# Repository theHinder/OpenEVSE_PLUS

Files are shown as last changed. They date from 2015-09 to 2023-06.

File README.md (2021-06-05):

# OpenEVSE_PLUS
README.md for OpenEVSE Hardware
Files SCH and BRD in Eagle format
License CC BY-SA 3.0
OpenEVSE Hardware

Current Version OpenEVSE_PLUS_v5.5.

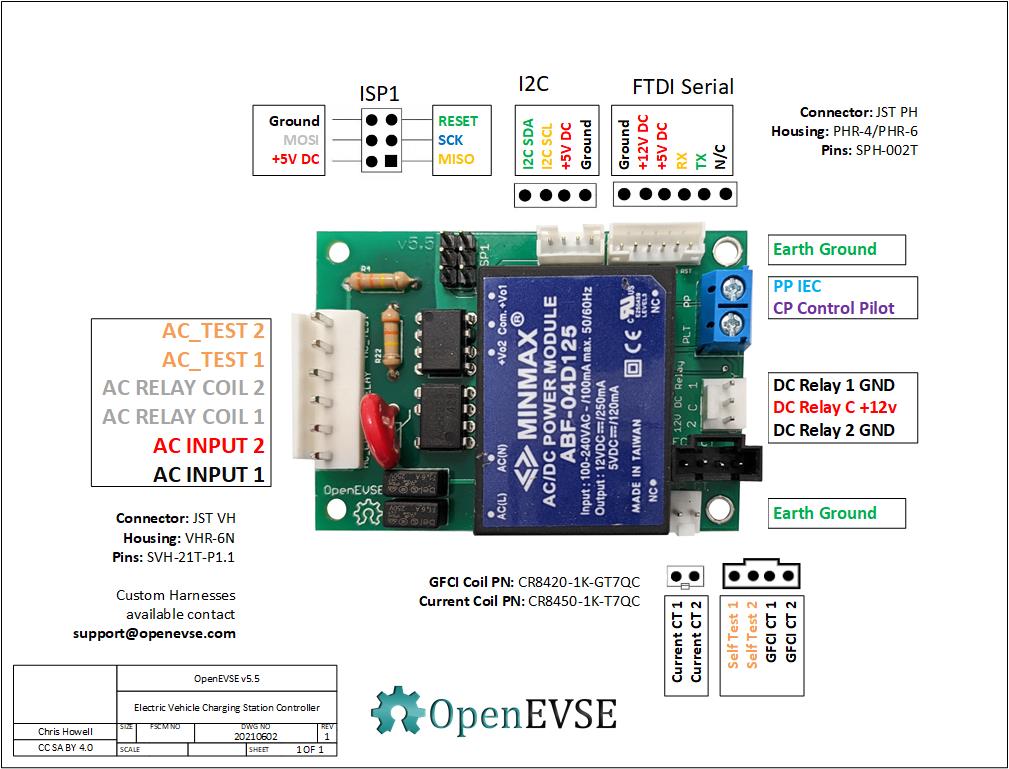
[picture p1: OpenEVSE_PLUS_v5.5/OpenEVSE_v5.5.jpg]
OpenEVSE Electric Vehicle controller v5.5 SAE J1772 IEC 61851


OpenEVSE_PLUS_V5.5 - Moved GFCI Test pin to enable move of DC Relay outputs to PWM capable pins supporting full power closing reduced power holding in OpenEVSE 7.1.2+ firmware. Added GPIO pin pulled HIGH to auto detect board version in software to automatically set new/old pin values without requiring different firmware. Replaced 0.1" generic non-polarized connectors with JST PH for Serial (WiFi) and i2c (Display). Combined power and data connections for WiFi to reduce eliminate a screw terminal connector and simplify wiring harness. Replaced DC/DC converter with a TC1044S invert chip to generate -12v from +12v. 

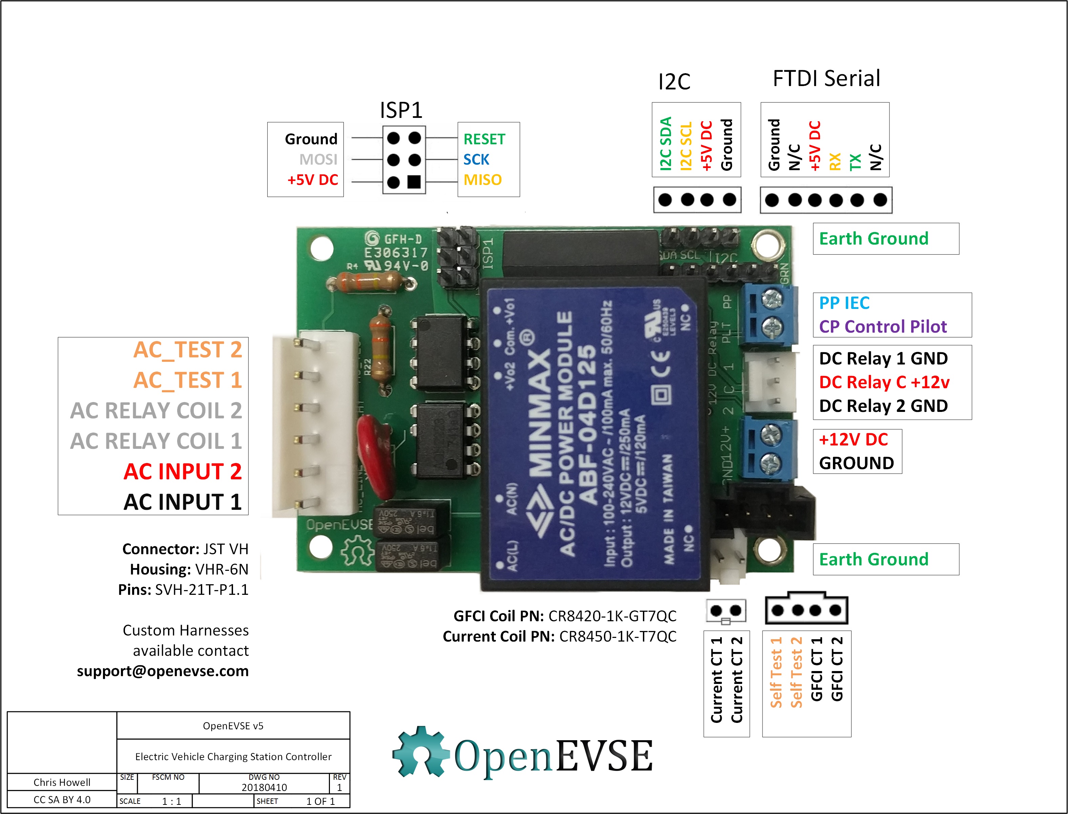
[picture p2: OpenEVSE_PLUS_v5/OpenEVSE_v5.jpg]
OpenEVSE Electric Vehicle controller v5 SAE J1772 IEC 61851


OpenEVSE_PLUS_v5 - Optimized for reduced build time and high volume manufacturing of changing stations, removed most screw terminals and replaced with common connectors. Change from 2 single chanel opto-isolators for AC detection to 1 dual channel. Added ground connections to screw holes.

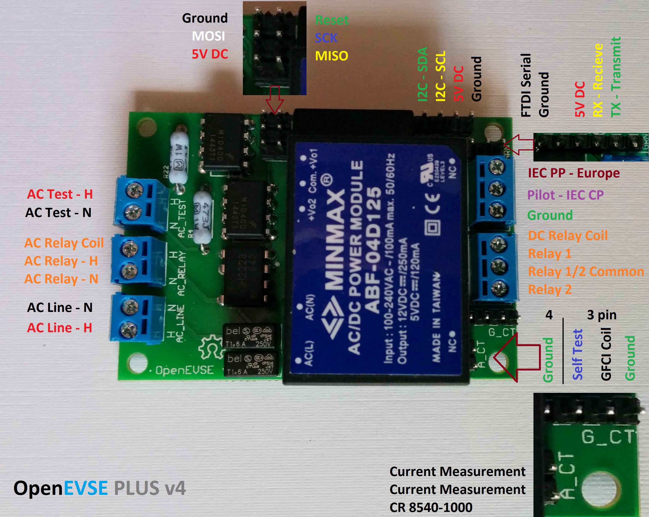
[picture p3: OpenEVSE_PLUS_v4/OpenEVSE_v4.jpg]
OpenEVSE Electric Vehicle controller v4 SAE J1772 IEC 61851


OpenEVSE_PLUS_v4 - Has 2 AC Detect chips like v1 + v2 plus the AC relay driver of v3. Added rectifier diodes to AC detect to improve detection in some conditions. Changed GFCI to individual pinout 4 pins.

OpenEVSE_PLUS_v3 - Removed 1 AC Detect chip and added AC relay driver. Added Current measurement circuit

OpenEVSE_PLUS_v2.5 - Added Current measurement circuit.

OpenEVSE_PLUS_v2 - modified GFCI pinout

OpenEVSE_PLUS_v1 - Inital version - Combined OpenEVSE v7 board and Advanced power supply into single board

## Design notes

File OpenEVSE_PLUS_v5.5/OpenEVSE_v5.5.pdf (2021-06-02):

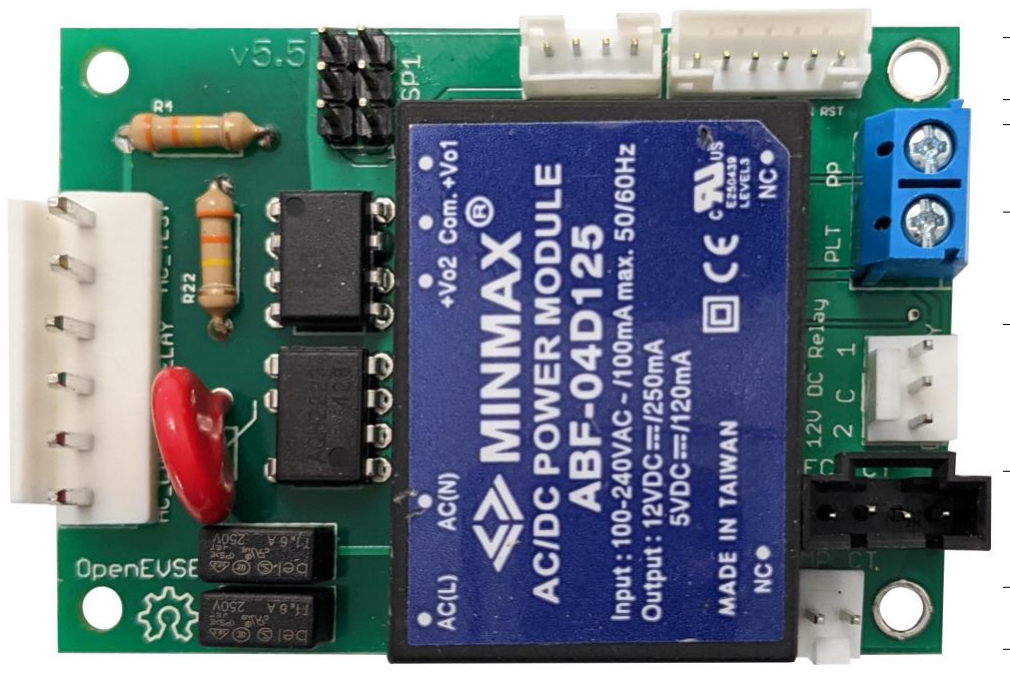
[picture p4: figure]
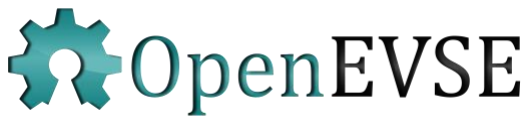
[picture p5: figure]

Chris Howell Chris Howell | SIZE SIZE | FSCM NO FSCM NO | DWG NO DWG NO | REV REV
| | | 20210602 20210602 | 1 1
CC SA BY 4.0 CC SA BY 4.0 | SCALE SCALE | | | SHEET SHEET | 1 OF 1 1 OF 1

OpenEVSE v5.5

Electric Vehicle Charging Station Controller

OpenEVSE v5.5

Electric Vehicle Charging Station Controller

## AC_TEST 2 AC_TEST 1 AC RELAY COIL 2 AC RELAY COIL 1 AC INPUT 2 AC INPUT 1

PP IEC
CP Control Pilot

### Earth Ground

### Earth Ground

### DC Relay 1 GND

DC Relay C +12v

### DC Relay 2 GND

I2C SDA
I2C SCL

+5V DC

Ground

Ground

+12V DC
+5V DC

RX
TX

N/C

I2C | FTDI Serial

RESET
SCK
MISO

Ground
MOSI
+5V DC

## ISP1

Current CT 1

Current CT 2

Self Test 1
Self Test 2

GFCI CT 1
GFCI CT 2

Connector: JST VH
Housing: VHR-6N
Pins: SVH-21T-P1.1

Custom Harnesses
available contact
support@openevse.com

GFCI Coil PN: CR8420-1K-GT7QC Current Coil PN: CR8450-1K-T7QC

Connector: JST PH
Housing: PHR-4/PHR-6
Pins: SPH-002T

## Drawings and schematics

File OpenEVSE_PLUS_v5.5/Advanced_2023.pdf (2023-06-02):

## LCD

## LCD

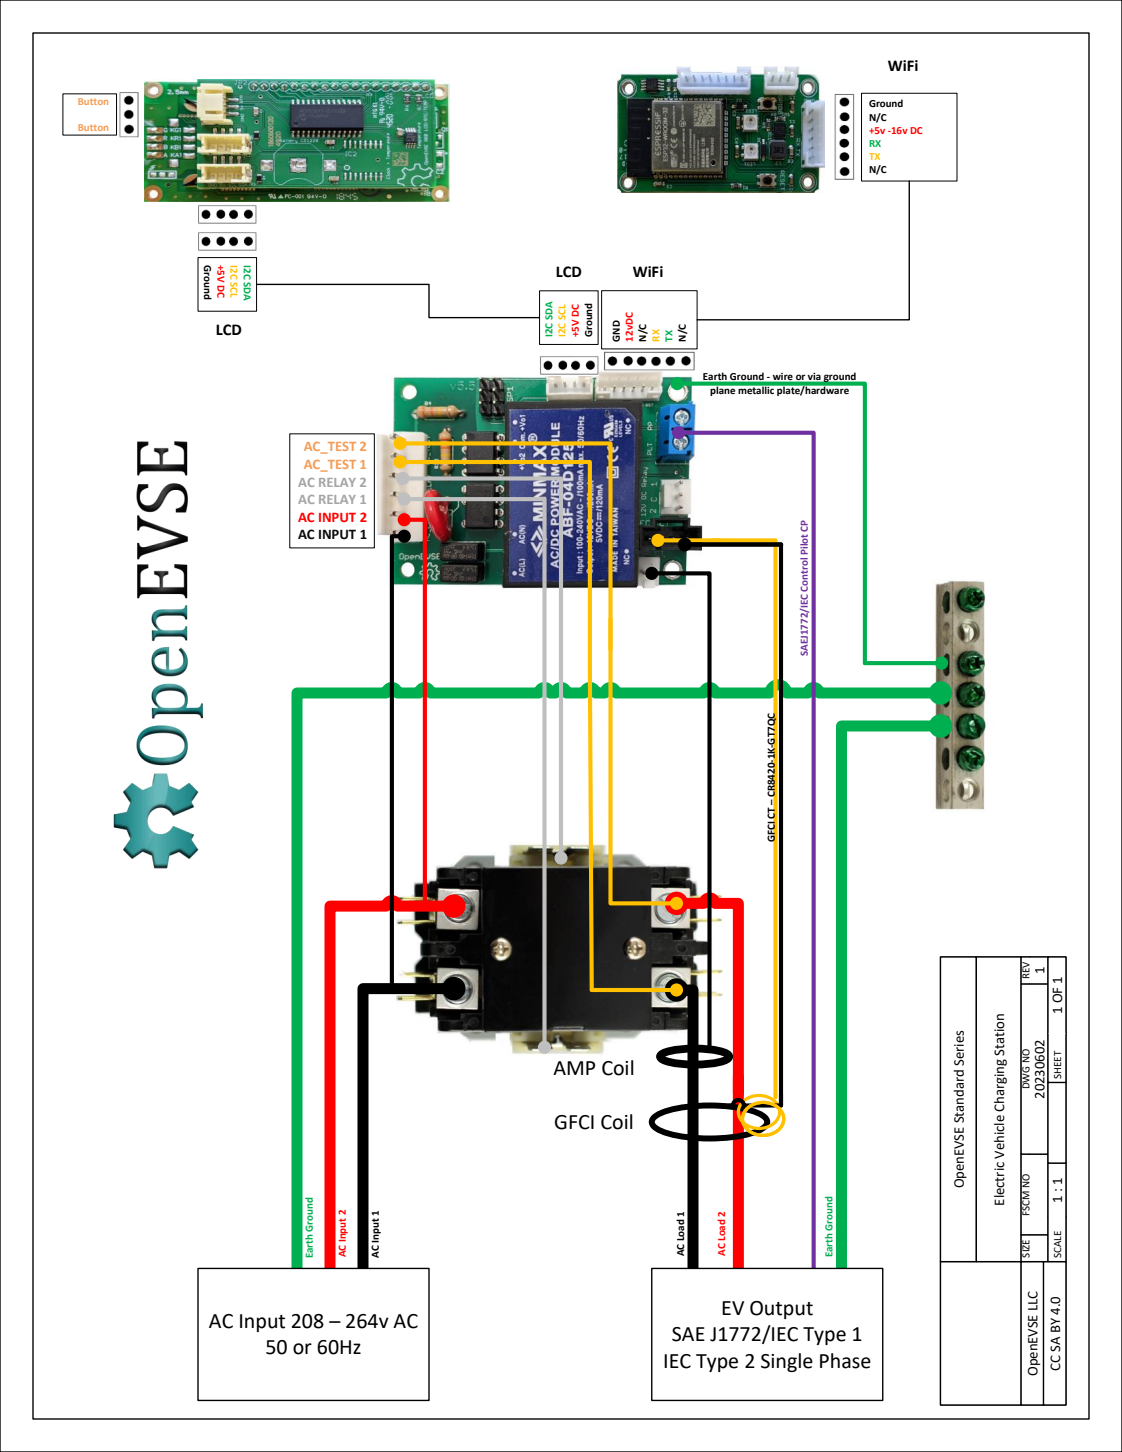
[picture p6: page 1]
I2C SDA; I2C SCL; Ground; Button; AC_TEST 2 AC_TEST 1 AC RELAY 2 AC RELAY 1 AC INPUT 2 AC INPUT 1; GFCI CT – CR8420-1K-GT7QC; Earth Ground; AC Input 2; AC Input 1; AC Load 1; AC Load 2; OpenEVSE LLC; GND; 12vDC; WiFi; Ground N/C +5v -16v DC RX TX N/C; GFCI Coil; AMP Coil

Earth Ground - wire or via ground
plane metallic plate/hardware

SAEJ1772/IEC Control Pilot CP

SIZE FSCM NO DWG NO REV

SCALE 1 : 1 SHEET 1 OF 1

Electric Vehicle Charging Station

OpenEVSE Standard Series

AC Input 208 – 264v AC

EV Output
SAE J1772/IEC Type 1
IEC Type 2 Single Phase

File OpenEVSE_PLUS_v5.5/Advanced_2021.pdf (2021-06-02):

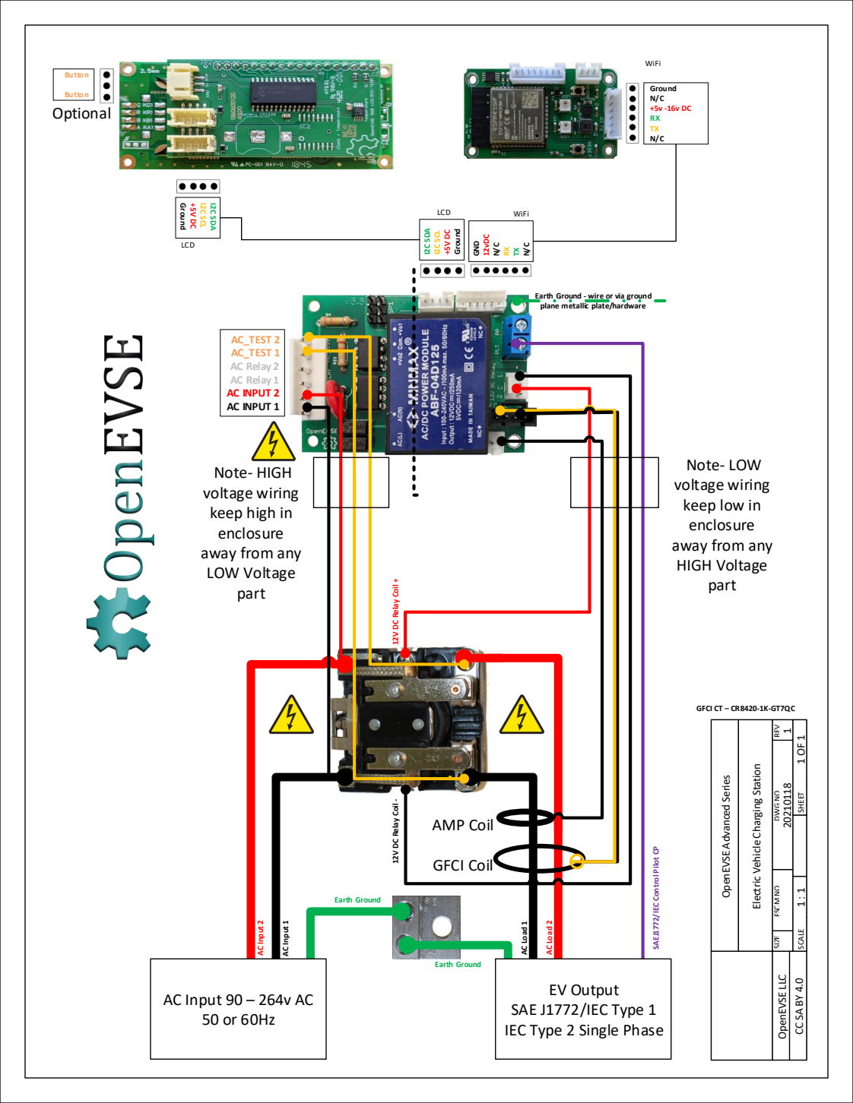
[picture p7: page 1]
I2C SDA; I2C SCL; Ground; GND; 12vDC; LCD; WiFi; Button; Ground N/C +5v -16v DC RX TX N/C; AC_TEST 2 AC_TEST 1 AC Relay 2 AC Relay 1 AC INPUT 2 AC INPUT 1; GFCI CT – CR8420-1K-GT7QC; AC Input 2; AC Input 1; AC Load 1; AC Load 2; Earth Ground; OpenEVSE LLC; Optional; GFCI Coil; AMP Coil

Earth Ground - wire or via ground
plane metallic plate/hardware

Note- LOW
voltage wiring
keep low in
enclosure
away from any
HIGH Voltage
part

Note- HIGH
keep high in
LOW Voltage

12V DC Relay Coil + 12V DC Relay Coil -

SIZE FSCM NO DWG NO REV

SCALE 1 : 1 SHEET 1 OF 1

Electric Vehicle Charging Station

OpenEVSE Advanced Series

SAEJ1772/IEC Control Pilot CP

EV Output
SAE J1772/IEC Type 1
IEC Type 2 Single Phase

AC Input 90 – 264v AC

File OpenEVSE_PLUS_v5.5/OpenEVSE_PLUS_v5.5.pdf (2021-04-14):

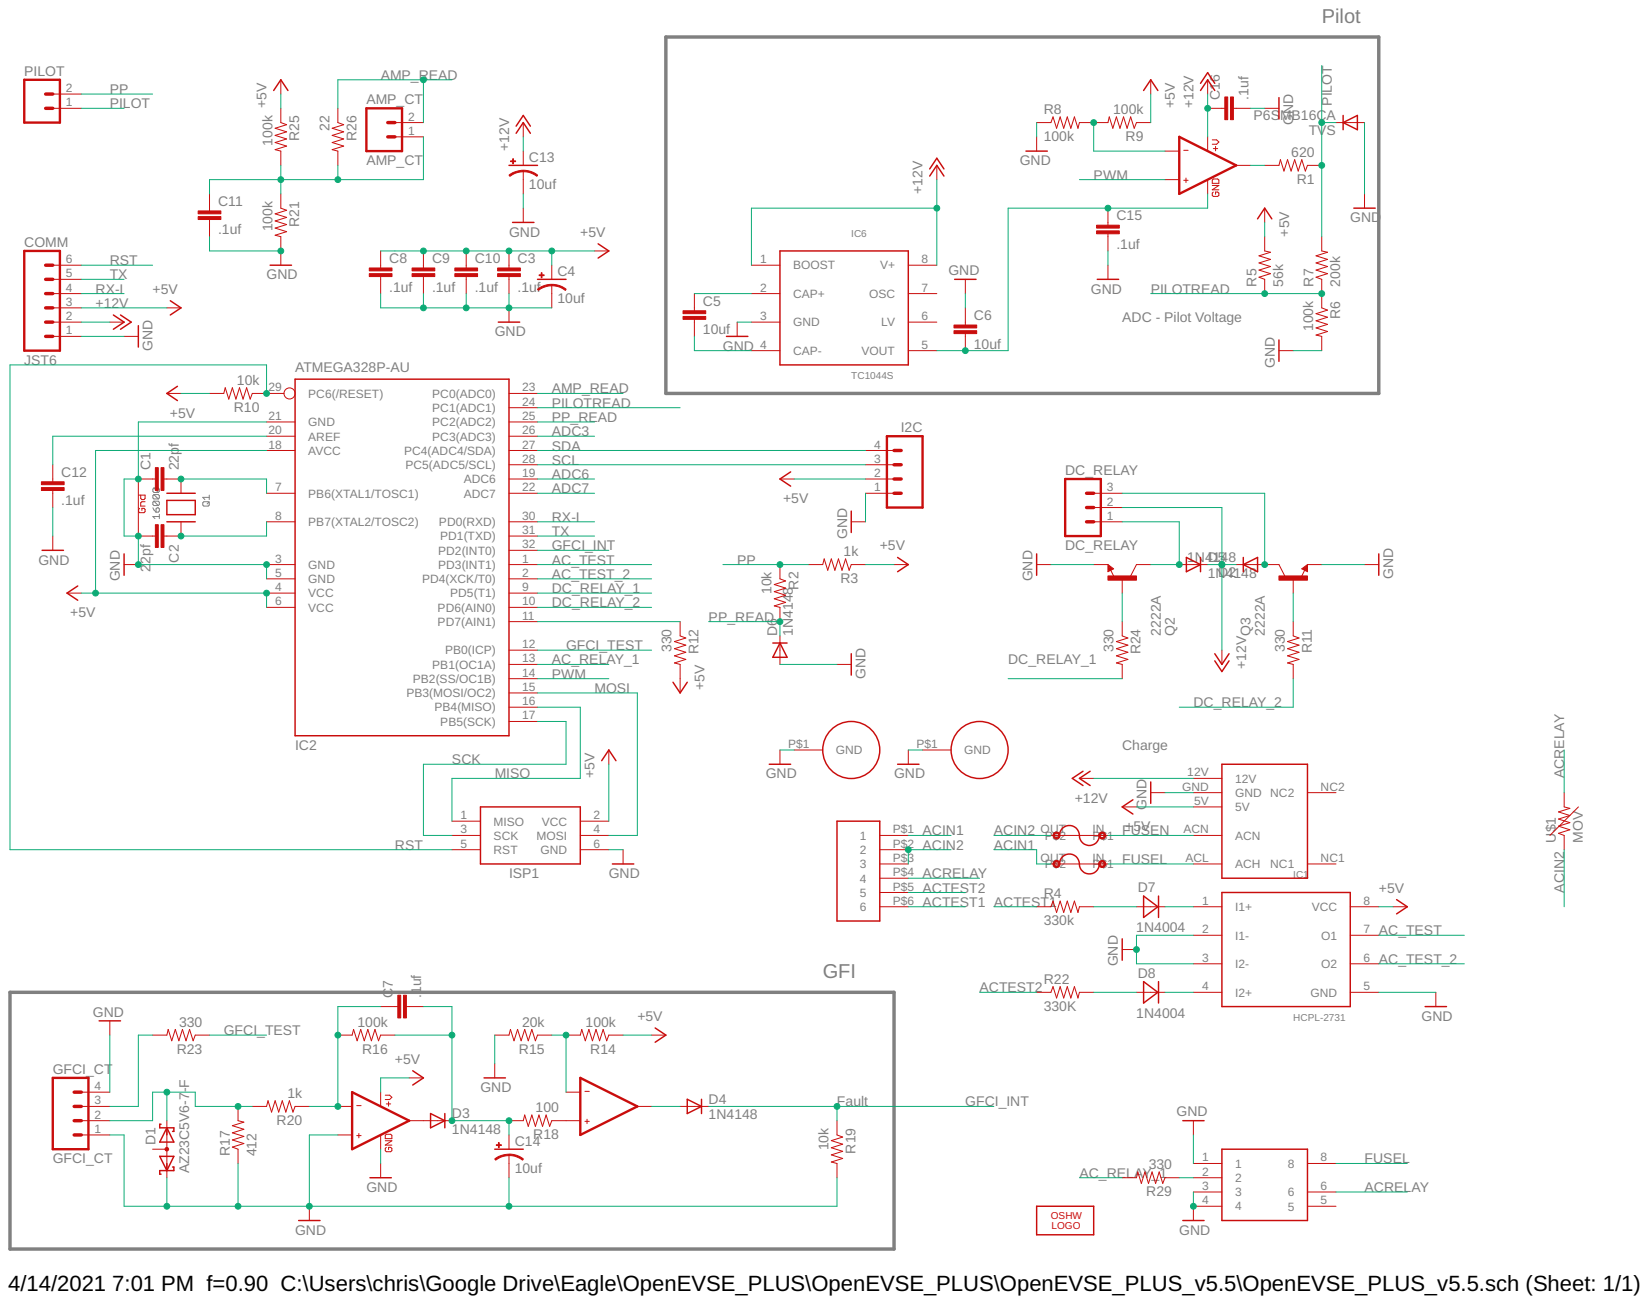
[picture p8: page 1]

4/14/2021 7:01 PM f=0.90 C:\Users\chris\Google Drive\Eagle\OpenEVSE_PLUS\OpenEVSE_PLUS\OpenEVSE_PLUS_v5.5\OpenEVSE_PLUS_v5.5.sch (Sheet: 1/1)

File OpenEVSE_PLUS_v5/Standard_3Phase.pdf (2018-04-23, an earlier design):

## Optional Cable Lock

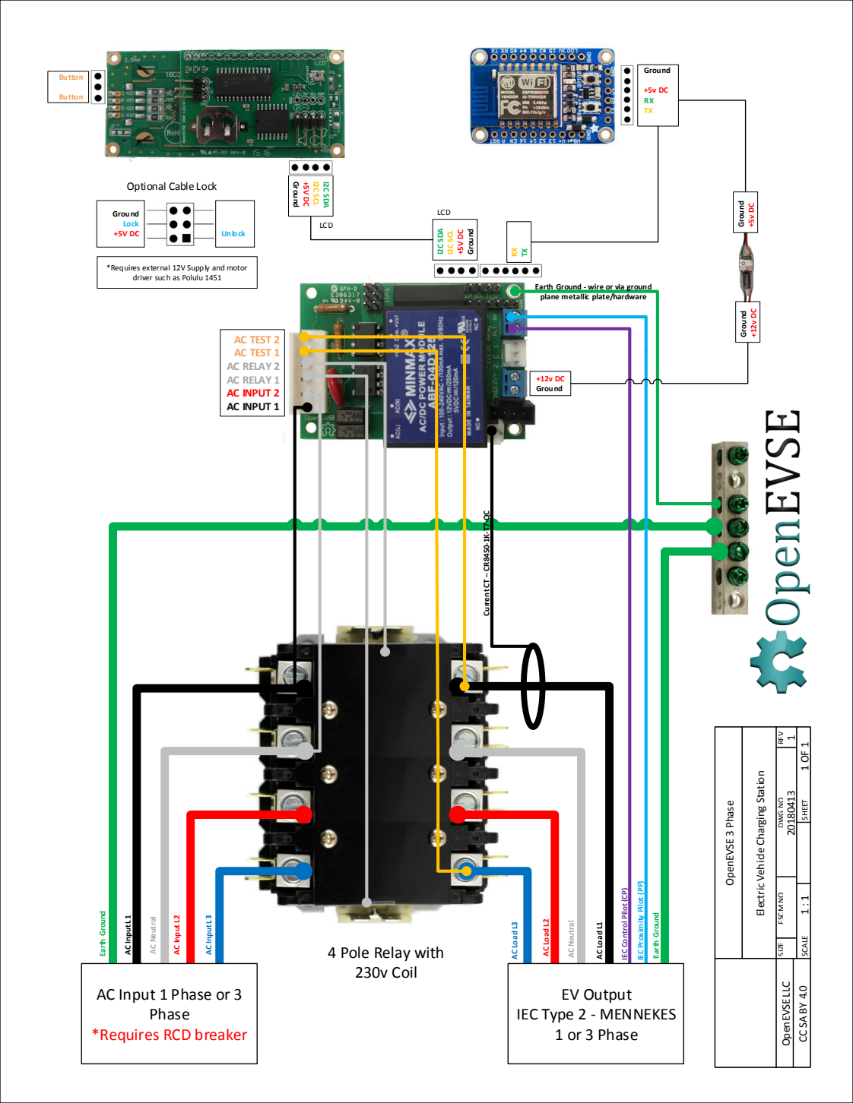
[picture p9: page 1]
I2C SDA; I2C SCL; Ground; LCD; Button; AC TEST 2 AC TEST 1 AC RELAY 2 AC RELAY 1 AC INPUT 2 AC INPUT 1; AC Neutral; AC Load L1; Earth Ground; AC Input L1; AC Load L2; OpenEVSE LLC; OpenEVSE 3 Phase; Phase; *Requires RCD breaker AC Input L2; AC Input L3; AC Load L3; +12v DC Ground; Unlock; Ground Lock +5V DC

*Requires external 12V Supply and motor

driver such as Polulu 1451

Earth Ground - wire or via ground
plane metallic plate/hardware

Current CT – CR8450-1K-T7-QC

SIZE FSCM NO DWG NO REV

SCALE 1 : 1 SHEET 1 OF 1

Electric Vehicle Charging Station

IEC Proximity Pilot (PP)

IEC Control Pilot (CP)

4 Pole Relay with
230v Coil

AC Input 1 Phase or 3

EV Output
IEC Type 2 - MENNEKES | 1 or 3 Phase

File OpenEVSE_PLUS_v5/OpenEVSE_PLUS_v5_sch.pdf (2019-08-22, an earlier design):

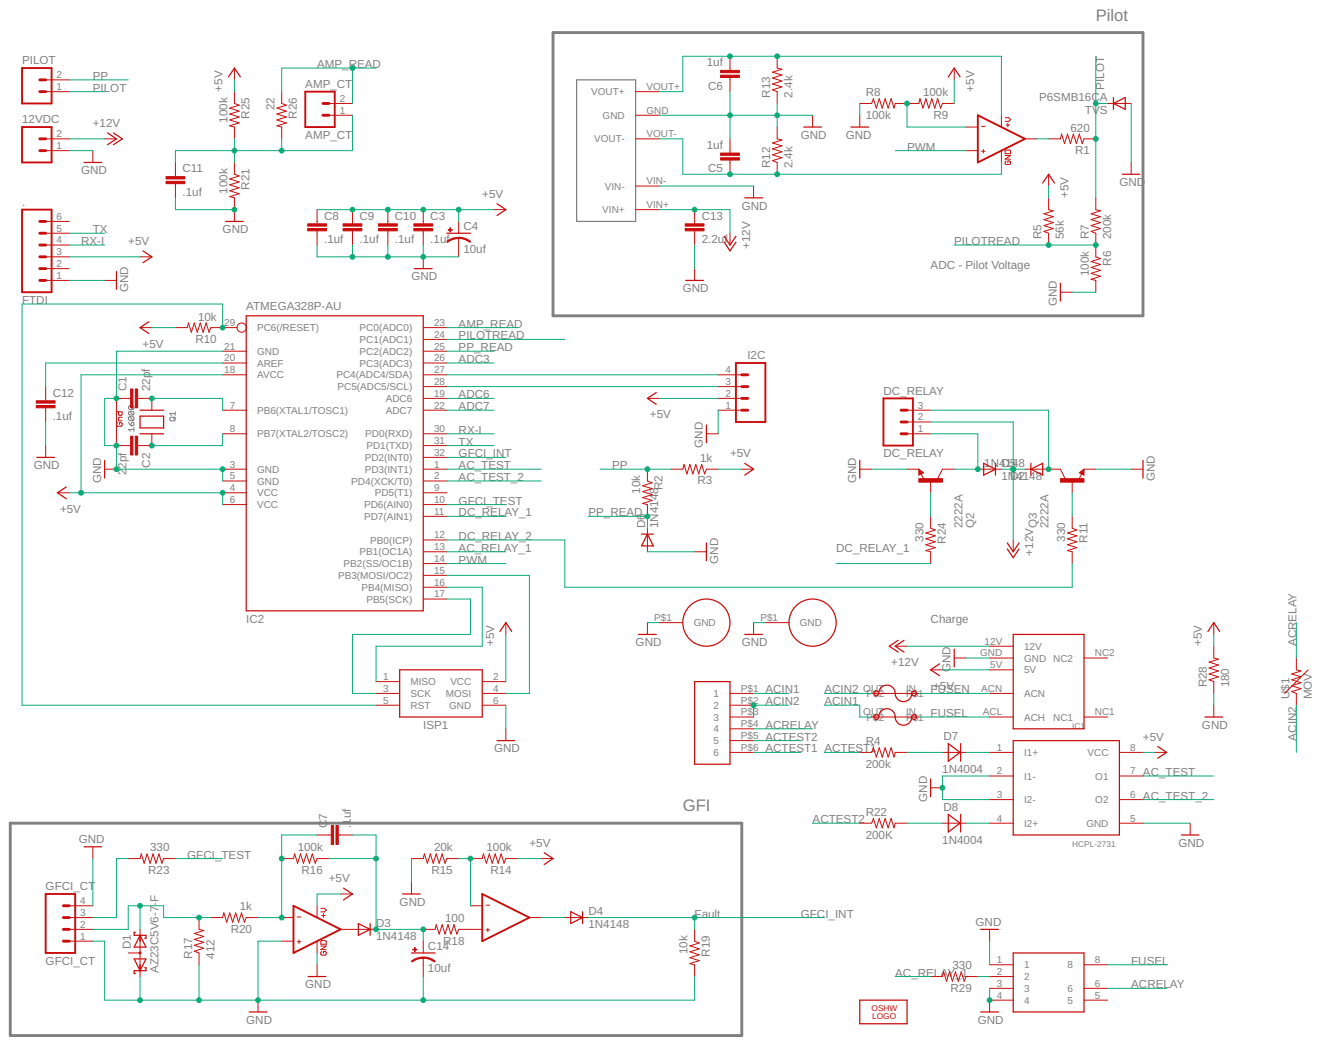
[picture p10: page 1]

PB6(XTAL1/TOSC1) 7

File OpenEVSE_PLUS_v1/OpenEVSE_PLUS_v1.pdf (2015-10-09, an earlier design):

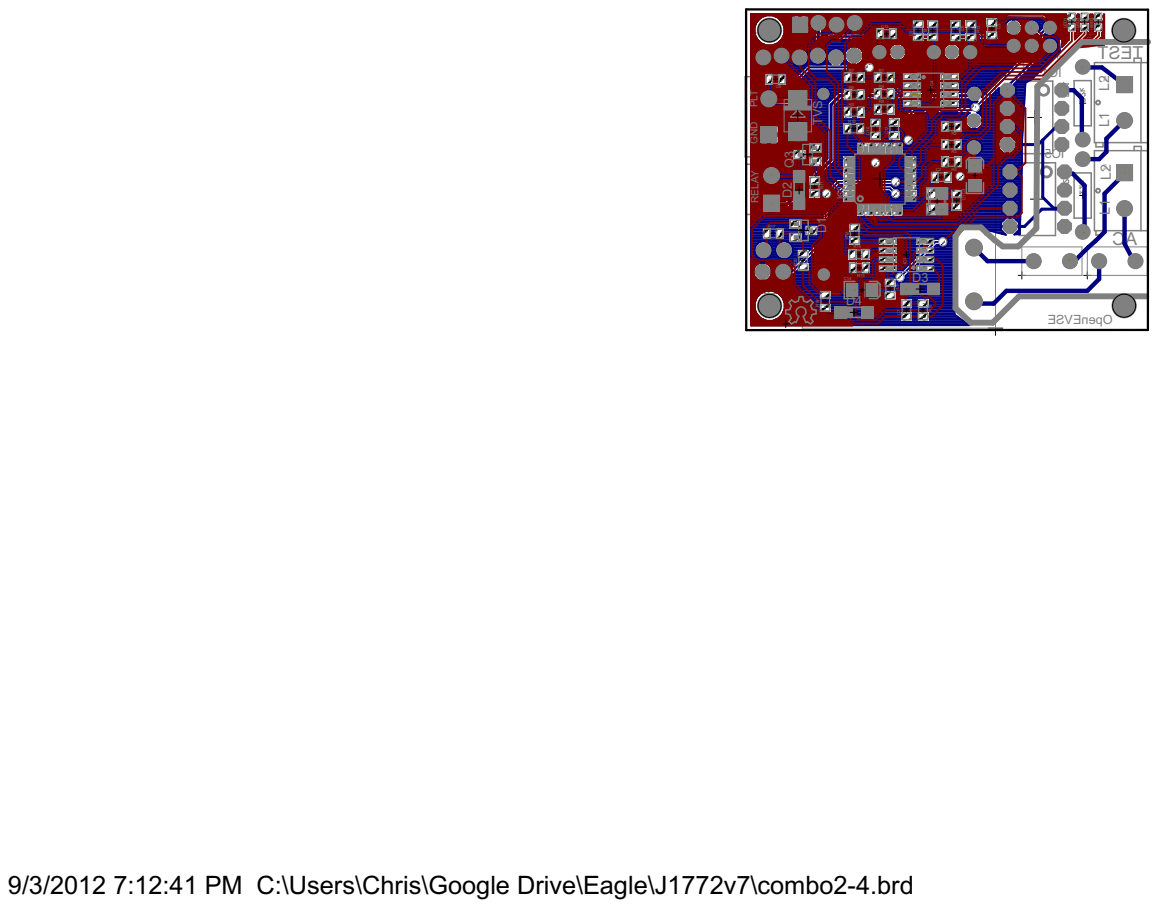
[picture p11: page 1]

9/3/2012 7:12:41 PM C:\Users\Chris\Google Drive\Eagle\J1772v7\combo2-4.brd

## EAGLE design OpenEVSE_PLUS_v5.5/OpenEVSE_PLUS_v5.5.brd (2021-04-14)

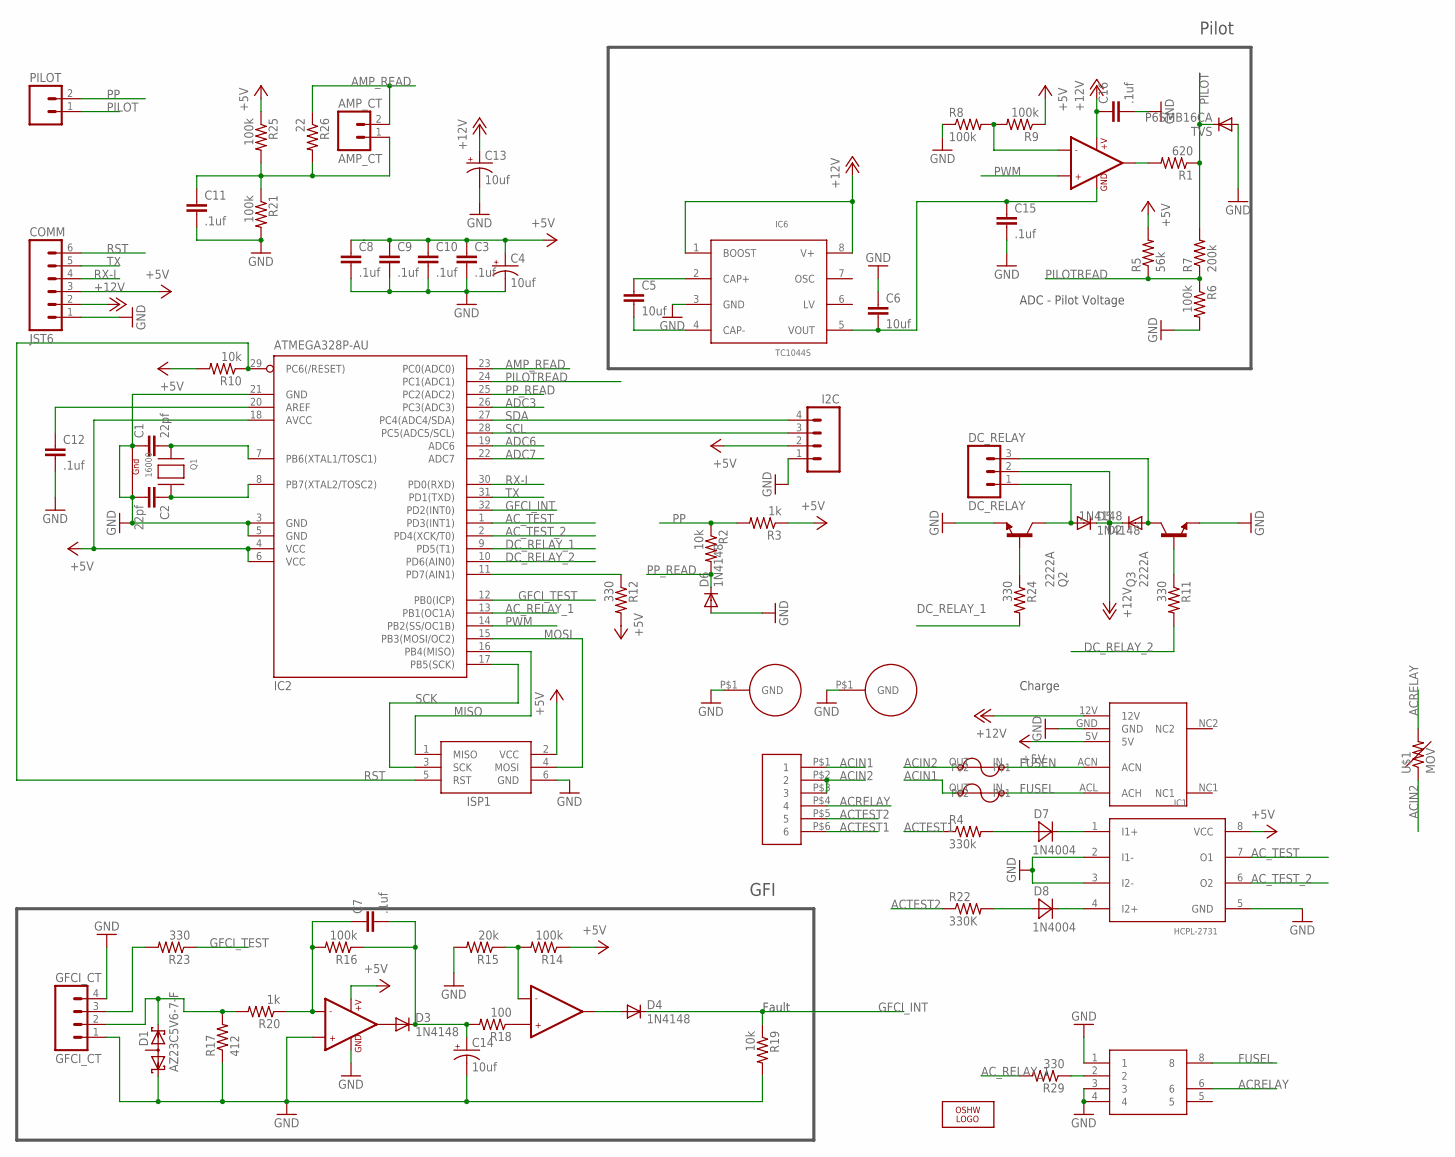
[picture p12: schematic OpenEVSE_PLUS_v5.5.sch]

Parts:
AC: JST-VH-6
AMP_CT: AMP_CT; MOLEX_2
C1, C2: 22pf; 0805
C3, C7, C8, C9, C10, C11, C12, C15, C16: .1uf; 0805
C4, C13, C14: 10uf; EIA3216
C5, C6: 10uf; 1206-CAP
COMM: JST6
D1: AZ23C5V6-7-F; SOT23
D2, D3, D4, D5, D6: 1N4148; SOD123
D7, D8: 1N4004; SMA
DC_RELAY: DC_RELAY; MOLEX_3
F1, F2: BEL1AFUSE; BELFUSE1A
GFCI_CT: GFCI_CT; GFCI_4
I2C: M04JST-PTH-VERT; JST-4-PTH-VERT
IC1: HCPL-2731; DIP08
IC2: ATMEGA328P-AU; TQFP32-08
IC3: LM358; SO08
IC4: LF353; SO08
IC5: AQH1213; DIP7
IC6: TC1044S; SO-8
ISP1: AVRISP-6; AVRISP
LOGO1: OSHW_LOGO_8MILX0150-NT; OSHW_8X150_NOTEXT
PILOT: M025MM; SCREWTERMINAL-5MM-2
PS1: MPM-04E-1205
Q1: 16000; NX3225
Q2, Q3: 2222A; SOT23
R1: 620; 0805
R2, R10, R19: 10k; 0805
R3, R20: 1k; 0805
R4: 330k; AXIAL-0.4
R5: 56k; 0805
R6, R8, R9, R14, R16, R21, R25: 100k; 0805
R7: 200k; 0805
R11, R12, R23, R24, R29: 330; 0805
R15: 20k; 0805
R17: 412; 0805
R18: 100; 0805
R22: 330K; AXIAL-0.4
R26: 22; 0805
TVS: P6SMB16CA; SMB
U$1: MOV
U$3, U$4: HOLE

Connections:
+5V: C3.1, C4.A (+), C8.1, C9.1, C10.1, COMM.3, I2C.2, IC1.8 (VCC), IC2.4 (VCC), IC2.6 (VCC), IC2.18 (AVCC), IC3.8 (+V), ISP1.2 (VCC), PS1.5V, R3.1, R5.2, R9.1, R10.2, R12.2, R14.1, R25.1
+12V: C13.A (+), C16.1, COMM.2, D2.C, D5.C, DC_RELAY.2, IC4.8 (+V), IC6.1 (BOOST), IC6.8 (V+), PS1.12V
-12V: C6.2, C15.1, IC4.4 (GND), IC6.5 (VOUT)
ACIN1: AC.P$1 (1), F2.OUT
ACIN2: AC.P$2 (2), AC.P$3 (3), F1.OUT, U$1.P$1 (1)
ACRELAY: AC.P$4 (4), IC5.6, U$1.P$2 (2)
ACTEST1: AC.P$6 (6), R4.P$1 (1)
ACTEST2: AC.P$5 (5), R22.P$1 (1)
AC_RELAY_1: IC2.13 (PB1(OC1A)), R29.2
AC_TEST: IC1.7 (O1), IC2.1 (PD3(INT1))
AC_TEST_2: IC1.6 (O2), IC2.2 (PD4(XCK/T0))
ADC3: IC2.26 (PC3(ADC3))
ADC6: IC2.19 (ADC6)
ADC7: IC2.22 (ADC7)
AMP_READ: AMP_CT.2, IC2.23 (PC0(ADC0)), R26.1
DC_RELAY_1: IC2.9 (PD5(T1)), R24.2
DC_RELAY_2: IC2.10 (PD6(AIN0)), R11.2
FUSEL: F2.IN, IC5.8, PS1.ACL (ACH)
FUSEN: F1.IN, PS1.ACN
GFCI_INT: D4.C, IC2.32 (PD2(INT0)), R19.1
GFCI_TEST: IC2.12 (PB0(ICP)), R23.1
GND: C1.1, C2.2, C3.2, C4.C (-), C6.1, C8.2, C9.2, C10.2, C11.2, C12.2, C13.C (-), C14.C (-), C15.2, C16.2, COMM.1, D1.1 (K1), D6.A, GFCI_CT.1, GFCI_CT.4, I2C.1, IC1.2 (I1-), IC1.3 (I2-), IC1.5 (GND), IC2.3 (GND), IC2.5 (GND), IC2.21 (GND), IC3.3 (+IN1), IC3.4 (GND), IC5.1, IC5.3, IC5.4, IC6.3 (GND), ISP1.6 (GND), PS1.GND, Q1.1 (G1), Q1.3 (G2), Q2.2 (E), Q3.2 (E), R6.2, R8.1, R15.2, R17.1, R19.2, R21.2, TVS.A, U$3.P$1, U$4.P$1
MISO: IC2.16 (PB4(MISO)), ISP1.1 (MISO)
MOSI: IC2.15 (PB3(MOSI/OC2)), ISP1.4 (MOSI)
unnamed: D2.A, DC_RELAY.3, Q3.3 (C)
unnamed: Q3.1 (B), R11.1
unnamed: C1.2, IC2.7 (PB6(XTAL1/TOSC1)), Q1.2 (X1)
unnamed: C2.1, IC2.8 (PB7(XTAL2/TOSC2)), Q1.4 (X2)
unnamed: D5.A, DC_RELAY.1, Q2.3 (C)
unnamed: AMP_CT.1, C11.1, R21.1, R25.2, R26.2
unnamed: C7.1, IC3.2 (-IN1), R16.2, R20.1
unnamed: D7.A, R4.P$2 (2)
unnamed: IC4.2 (-IN1), R8.2, R9.2
unnamed: IC4.1 (OUT1), R1.2
unnamed: D7.C, IC1.1 (I1+)
unnamed: D8.C, IC1.4 (I2+)
unnamed: D8.A, R22.P$2 (2)
unnamed: IC5.2, R29.1
unnamed: C5.1, IC6.2 (CAP+)
unnamed: D1.2 (K2), GFCI_CT.2, R17.2, R20.2
unnamed: D3.A, IC3.1 (OUT1)
unnamed: GFCI_CT.3, R23.2
unnamed: C7.2, C14.A (+), D3.C, R16.1, R18.2
unnamed: IC3.6 (-IN2), R14.2, R15.1
unnamed: D4.A, IC3.7 (OUT2)
unnamed: IC3.5 (+IN2), R18.1
unnamed: C5.2, IC6.4 (CAP-)
unnamed: IC2.11 (PD7(AIN1)), R12.1
unnamed: Q2.1 (B), R24.1
unnamed: C12.1, IC2.20 (AREF)
PILOT: PILOT.1, R1.1, R7.2, TVS.C
PILOTREAD: IC2.24 (PC1(ADC1)), R5.1, R6.1, R7.1
PP: PILOT.2, R2.1, R3.2
PP_READ: D6.C, IC2.25 (PC2(ADC2)), R2.2
PWM: IC2.14 (PB2(SS/OC1B)), IC4.3 (+IN1)
RST: COMM.6, IC2.29 (PC6(/RESET)), ISP1.5 (RST), R10.1
RX-I: COMM.4, IC2.30 (PD0(RXD))
SCK: IC2.17 (PB5(SCK)), ISP1.3 (SCK)
SCL: I2C.3, IC2.28 (PC5(ADC5/SCL))
SDA: I2C.4, IC2.27 (PC4(ADC4/SDA))
TX: COMM.5, IC2.31 (PD1(TXD))

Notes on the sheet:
Pilot
ADC - Pilot Voltage
Charge
Fault
GFI

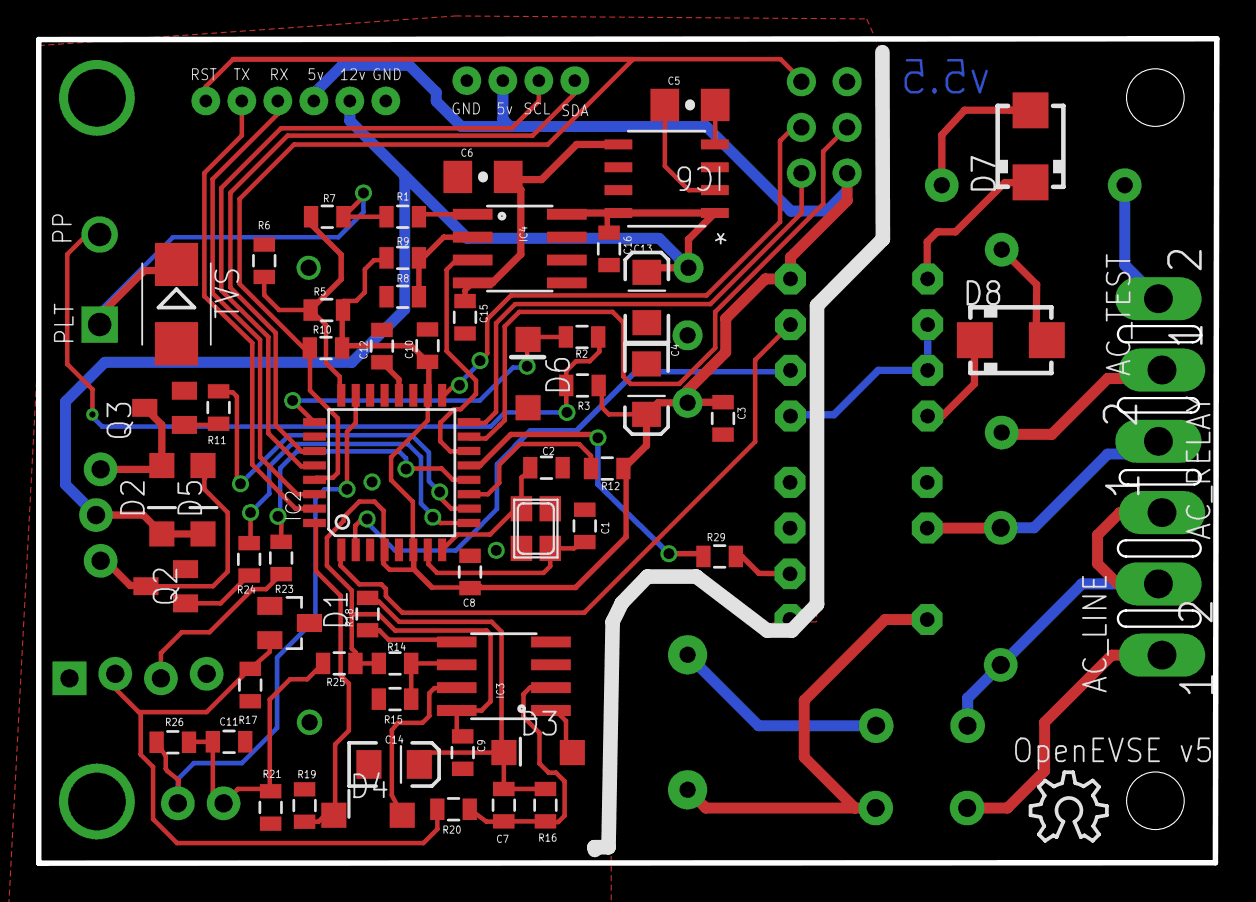
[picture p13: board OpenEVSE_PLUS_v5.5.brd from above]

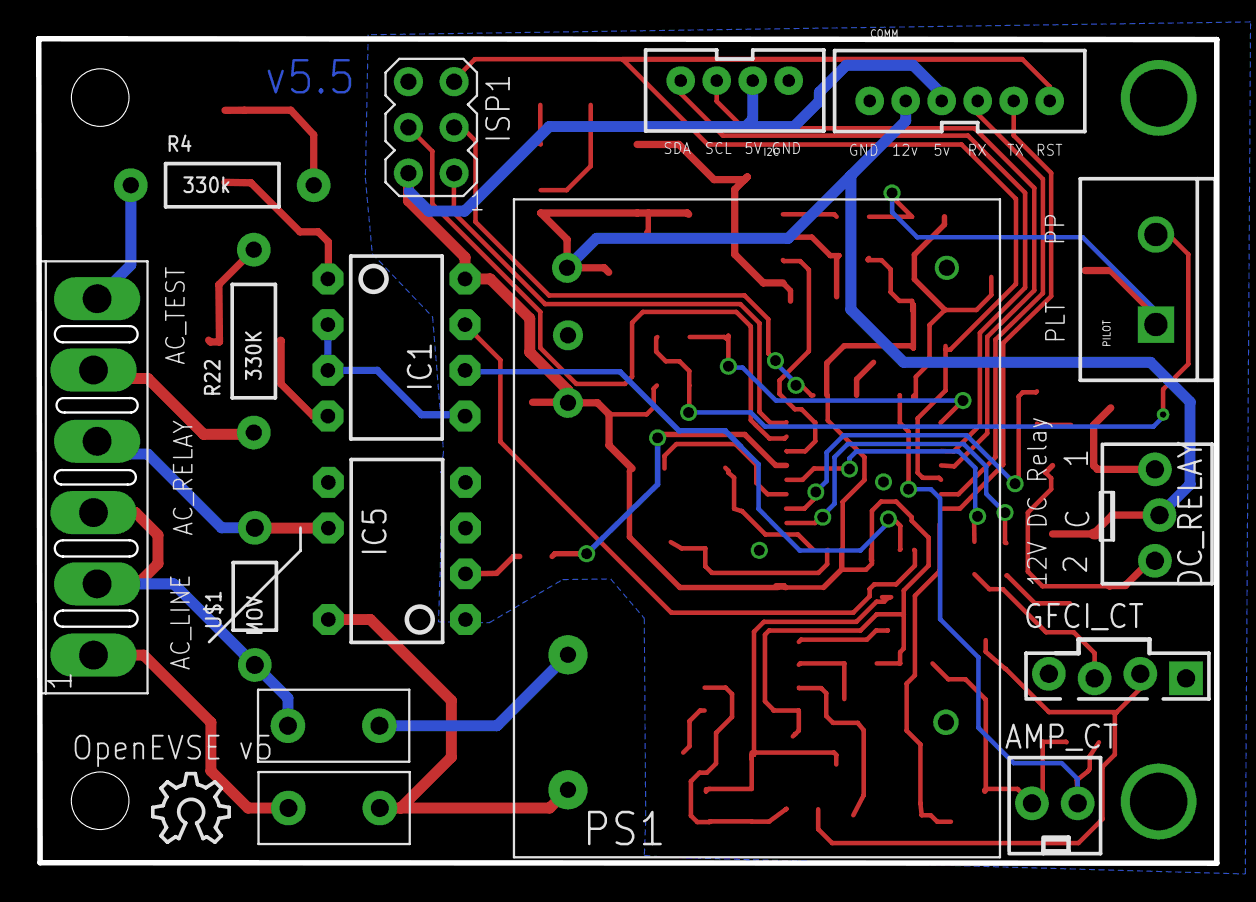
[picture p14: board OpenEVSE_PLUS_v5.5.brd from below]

Board: 2 copper layers, 65.4 x 45.8 mm, 76 parts (17 on the bottom side), 58 nets.

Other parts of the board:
LOGO2: OSHW_LOGO_8MILX0150-NT; OSHW_8X150_NOTEXT

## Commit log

2015-09-30 OpenEVSE_PLUS
    Move all source files from google code and web files
    [OpenEVSE_PLUS_v2.5.brd, OpenEVSE_PLUS_v2.5.sch, OpenEVSE_PLUS_v2.brd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]
2015-10-09 OpenEVSE Plus v1
    [OpenEVSE_PLUS_v1.brd, OpenEVSE_PLUS_v1.sch]
2017-04-11 Updates to components
    Updated parts values so generic footprints report the correct part when exporting Eagle generated BOM.
    IC2 value 328P
    IC3 value LM358
    IC4 value LF353
    TVS value P6SMB16CA
    D1 value AZ23C5V6-7-F
    DC/DC value MD112D-12E
    [OpenEVSE_PLUS_v4.brd, OpenEVSE_PLUS_v4.sch]
2018-04-10 v5
    V5 files added
    [OpenEVSE_PLUS_v5.brd, OpenEVSE_PLUS_v5.sch]
2018-05-22 Update Connection Diagram
    update to include part numbers for JST VH Housing and Pins and OpenEVSE GFCI and current coils
2019-03-25 added pdf version of schematic
2019-03-25 changed pdf version of file name to not clash on non-case sensative operating systems
2021-04-14 Upload files for OpenEVSE PLUS v 5.5
    Upload source files for OpenEVSE PLUS v 5.5
    [OpenEVSE_PLUS_v5.5.brd, OpenEVSE_PLUS_v5.5.sch]

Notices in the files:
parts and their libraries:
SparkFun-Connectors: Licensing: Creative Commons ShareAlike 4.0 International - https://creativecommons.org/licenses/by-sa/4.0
